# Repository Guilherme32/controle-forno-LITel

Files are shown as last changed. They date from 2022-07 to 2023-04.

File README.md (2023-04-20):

# Controle do forno do LITel

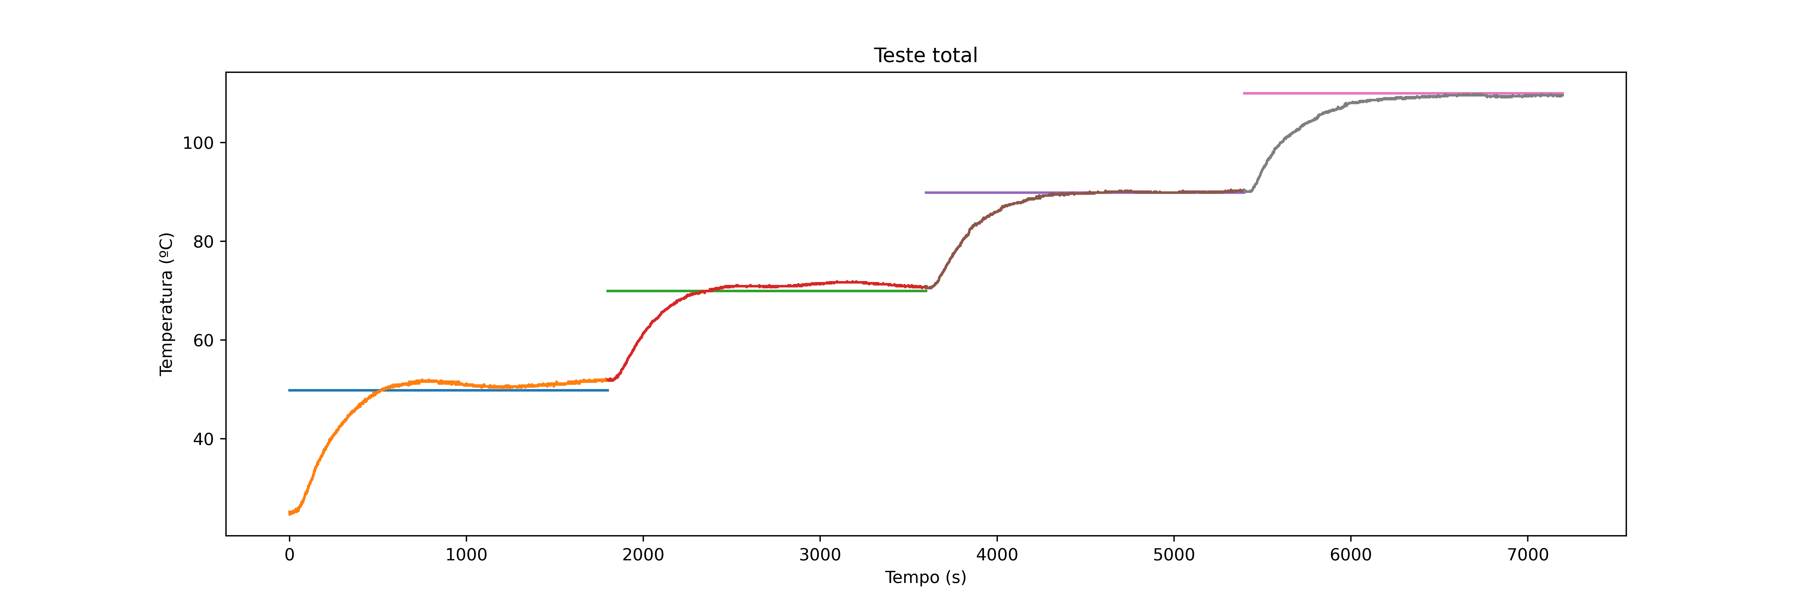
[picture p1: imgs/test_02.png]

Último teste realizado (14/10/2022)

Esse repositório guarda o que foi desenvolvido para o controle do forno do
Laboratório de Instrumentação e Telemetria da UFJF (LITel)

# Informações

O sistema funciona aplicando um controle por lógica Fuzzy (FLC), com modulação
de potência por detecção de zero, para manter a temperatura vista pelo sensor
central do forno no valor especificado. Também pode funcionar por potência fixa.

> Este README contém algumas informações básicas do controlador, e uma
explicação das interfaces de comunicação. *Assim, possui o necessário para
utilizar o projeto*. Maiores detalhes do funcionamento de outras partes podem
ser encontradas no **manual.md** e também na documentação dos códigos.

Para interação com o usuário existem duas interfaces de comunicação:
- WiFi
- Serial

# Comunicação WiFi

Para se comunicar com o controlador por wifi, basta estar na mesma rede. Para
isso, deve-se conectar no ponto de acesso do esp ou estar na rede em que ele
estiver conectado.

Uma vez conectado à mesma rede do esp, o programa pode ser controlado através
das páginas acessíveis em **http://\<endereço ip\>** ou  **\<endereço ip\>:80**.
O endereço depende de qual interface wifi está sendo utilizada.

## Ponto de Acesso (Access Point)

O esp está configurado para funcionar em modo "access point", permitindo que
dispositivos se conectem a ele. As credenciais de acesso são:

> SSID: forno-litel
>
> Senha: 787Cu7kg

Nesse modo, o programa pode ser acessado pelo ip:

> ip: 192.168.4.1

## Modo Estação (station)

Nesse modo, o esp tentará se conectar à rede que estiver configurado para se
conectar. A única forma de alterar essa configuração é pelas próprias páginas
web.

> Ao mudar a configuração, ele automaticamente irá se desconectar da rede em
que estava anteriormente. Logo a forma mais indicada de fazer essa alteração é
acessando através do ponto de acesso.

O ip quando nesse modo depende do roteador (ou ponto de acesso no geral) em que
está se conectando. Esse ip será informado na página de conexão e também pode
ser descoberto pelo comando serial **!netinfo**.

## Páginas

### Página Principal

A página principal serve apenas como uma entrada à interface. Ela permite acesso
às outras páginas do sistema, e também linka para esse repositório.

> Todas as outras páginas possuem também links para as outras páginas do sistema
e para esse repositório.

### Conexão

Essa página mostra as informações de conexão (SSID, senha, ip), e permite mudar
as credenciais da rede a ser acessada pelo modo estação.

> No caso do modo estação, a página também indica se o esp está devidamente
conectado

### Controle

Essa é a página mais importante, e também a mais pesada. É normal que ela demore
muitos segundos para carregar.

> Se a página estiver apresentando instabilidades, por favor reporte para mim ou
crie um "issue" aqui no repositório

A página possui alguns componentes:

- Operação: 
    O forno pode funcionar por potência fixa ou por set point. Uma vez que
    o modo é selecionado, e o valor desejado inserido na caixa de texto, o botão
    enviar pode ser pressionado para enviar as informações para o
    microcontrolador.

- Informações instantâneas:
    Para melhor entendimento, algumas informações são colocadas referentes ao
    funcionamento do forno no último instante recebido.
    - A potência enviada às resistências;
    - Se o sistema está em regime transitório ou alcançou o estacionário;
    - A temperatura no sensor principal (S5, o que fica no centro).

- Gráfico:
    Um gráfico temporal com os valores de set point (se estiver no modo de
    controle) e os valores lidos por todos os sensores. Cada conjunto pode ser
    apagado ou redesenhado para maior clareza. Também, vale notar que o gráfico
    somente mostra as últimas 240 amostras.

> O gráfico e as informações instantâneas são atualizados com 5 segundos. Dessa
forma, o gráfico mostra amostras dos últimos 20 minutos.

# Comunicação Serial

A interface serial funciona utilizando uma taxa (baud rate) de **115200 bits/
s**, com 8 bits de dados e 1 de parada (stop bit).

A comunicação ocorre através de comandos. Para enviar um comando, deve-se enviar
primeiro um caracter de início (!), então escrever o comando, seguido pelo
argumento, caso exista, seguindo a formatação exigida.

Os comandos implementados são:
- **!netinfo**: Devolve as informações de rede:
    - SSID, senha e ip do modo ap;
    - Se estiver devidamente conectado no modo sta, SSID e IP desse modo;
    - Se não estiver, indica que o sta está desconectado;

- **!tempX**, onde X é o índice do sensor: Devolve a temperatura lida no sensor
de índice X;

- **!sensorX**, onde X é o índice do sensor: Parecido com o **temp**, mas
retorna o inteiro entre 0 e 1023 que representa a leitura crua do adc (analog -
digital converter) do esp;

- **!settXXX.X**, onde XXX.X é a temperatura em ºC, com três dígitos antes
da vírgula, e um depois: Seta o set point do sistema de controle para o valor
de temperatura passado. Para não alcançar a temperatura máxima de operação do
sensor, o valor máximo que pode ser passado é 140ºC. Automaticamente ativa o
modo de controle;

- **!setpXXX**, onde XXX é um inteiro representando a quantidade de semiciclos
ligados: Seta a relação de potência a ser enviada para as resistências. O
período da modulação de potência é de 120 semiciclos, logo o valor enviado deve
estar entre 0 e 120 (inclusivo), onde 0 é carga desligada e 120 é carga em plena
potência. Automaticamente ativa o modo de potência fixa;

> A formatação dos argumentos deve ser exatamente como descrita, ou o programa
pode não responder adequadamente

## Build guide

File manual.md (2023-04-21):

# Manual de Referência do Sistema de Controle Do Forno LITel

O sistema de controle foi desenvolvido com um microcontrolador, um esp8266,
programado em c com uso do sdk da fabricante com sistema operacional [ESP8266
RTOS SDK](https://github.com/espressif/ESP8266_RTOS_SDK). Para o desenvolvimento
da placa de circuito impresso (PCB), foi utilizado o
[KiCad](https://www.kicad.org), um programa de Automação de Design Eletrônico
(EDA) open source.

A parte física pode ser dividida em algumas seções, que foram também separadas
para maior clareza no esquemático do circuito (kicad/projeto/projeto.kicad_sch):

# Divisão da parte física

## Sensor

O esp8266 possui apenas um conversor analógico - digital (adc), portanto foi
necessário o uso de um multiplexador analógico (CD4051) para permitir a leitura
de todos os sensores. Também, o adc suporta até 1V, enquanto o sensor pode
enviar até 1.5V. Um divisor de tensão foi utilizado para reduzir essa pela
metade, se encaixando com folga nos limites do microcontrolador.

O adc possui uma precisão de 10 bits, ou 1024 valores. Isso significa uma
precisão de 1/1024 = 0.977mV. O sensor utilizado (LM35) entrega 10mV/ºC, com
precisão típica entre 0.2ºC -> 2mV e 0.4ºC -> 4mV.

Os sensores são:
- S1: Central do fundo
- S2: Lateral direito
- S3: Lateral esquerdo
- S4: Porta
- S5: Principal (centro)
- S6: Ambiente

> No software, os sensores são indexados a partir de 0, não 1, logo o índice
será o descrito aqui menos 1.

## Status

Para visualização de alguns parâmetros diretamente na placa, três leds são
utilizados:

- Steady State: Liga quando a temperatura alcança um regime permanente;

- Wifi Status: Indica o status do modo estação do esp. Enquanto está tentando se
conectar, o led pisca. Se falhar / enquanto não estiver conectado devidamente,
fica desligado. Quando ligado e funcionando, fica ligado;

- Ligado: Liga diretamente na linha de 3.3V da placa, indicando quando o sistema
está energizado.

## Botões (Buttons)

Alguns botões são necessários para o adequado funcionamento, principalmente
para desenvolvimento.

- Reset: O botão para resetar o esp;
- Exit: Esse botão é ligado no pino de flash do esp, que deve ser mantido
em nível lógico baixo (pressionado) ao ligar para permitir o upload de novo
firmware.

## Detecção de Zero (Zero Detection)

Para a estratégia de modulação implementada, é necessário que o microcontrolador
saiba exatamente quando a tensão CA cruza 0V. Essa seção do circuito utiliza
um diodo zener e um optoacoplador (4N25) para gerar um pulso exatamente nesse
momento.

> O diodo zener foi utilizado para aumentar a largura do pulso, que não estava
sendo detectado de forma consistente em testes com apenas o optoacoplador.

## Driver da Carga (Load Driver)

Essa parte é a responsável por ativar a resistência da saída, através do uso
de um optoacoplador, que permite a condução entre o Gate e o terminal A2,
logo ativando a condução do triac, quando recebe um sinal de nível alto do
microcontrolador.

## Alimentação (Power)

O circuito é alimentado com 5V, que pode vir tanto do conversor USB-serial (se
estiver sendo utilizado) quanto de uma alimentação externa com um conector CC de
2.5mm. Os capacitores são utilizados para reduzir ruído da fonte e para garantir
que, caso o microcontrolador consuma uma corrente mais alta do que a fonte /
conversor são capazes de suprir por um curto período de tempo, o circuito ainda
funcione.

> Embora o esperado seja 5V, a fonte pode ser de até 10V, e os circuito ainda
funcionará adequadamente. Porém, vale notar que, se o circuito for alimentado
por uma fonte externa, ele **não deve ser alimentado pela tensão do conversor
USB-serial**. Nesse caso ainda deve se ligar o gnd do serial.

A alimentação CA é para a carga, e é protegida por um fusível (o instalado na
montagem foi de 12A).

## Serial

Aqui há apenas a conexão direta entre os pinos de comunicação serial do
microcontrolador com dois pinos (TX, RX), e a conexão da alimentação também em
dois pinos (5V, GND)

> Ao longo de todo o circuito, estão presentes diversos jumpers. Esses foram
usados apenas para facilitar a construção da PCB

# O Software

Para o projeto, foram desenvolvidos códigos para o microcontrolador (software
embarcado), para automatizar tarefas, e para interface com o usuário com uma
página web.

O código da página web foi desenvolvido em html, css e js, apenas como um
supervisório, e os detalhes de seu conteúdo podem ser vistos nos README.md e
também nas documentações e comentários dentro dos códigos.

O código para automatizar o envio dos arquivos web para o esp está em codigo/
helpers.

O software embarcado foi todo desenvolvido para ser concorrente, por meio do
sistema operacional FreeRTOS, embutido no
[SDK utilizado](https://github.com/espressif/ESP8266_RTOS_SDK), a esp-idf
(SDK da fabricante). Cada parte do sistema foi implementada em um arquivo .c
separado, e todas são inicializadas no main.c. Para os sistemas que dependem de
uma task, essas também são criadas no main.

> Para mais detalhes em qualquer código, basta abrir e ler os comentários e
documentações das funções. As documentações se encontram nos headers (.h) para
funções públicas, e nos source (.c) para as estáticas.

- main: O ponto de entrada do programa do microprocessador. Inicializa cada
parte individual do sistema, e cria as tasks para os que precisam de uma criada;

- wifi: Cuida da conexão WiFi do esp8266, tanto a inicialização do modo *Access
Point* quanto de tentar conectar a uma rede externa no modo *Station*;

- sensor_reader: Responsável por fazer a leitura periódica dos sensores e manter
seus valores acessíveis a outras partes do programa;

- serial_comm: Trata as entradas recebidas na porta serial, e ativa os devidos
comandos quando os seus padrões forem detectados;

- server: Implementa o servidor HTTP que serve como interface principal do
sistema;

- storage_spiffs: Faz a inicialização (mount) do sistema de arquivos usado
(SPIFFS). O sistema de arquivos é utilizado apenas para guardar os arquivos
web;

- helpers: Possui funções independentes que podem ser úteis em diversas partes
do programa, apenas para evitar reescrevê-las;

## controller

Essa seção é responsável por enviar à carga a potência desejada, e também por
periodicamente invocar controlador propriamente dito (que toma a decisão). O
algoritmo de modulação de potência utilizado foi um baseado no por detecção
de zero (*Zero Detection*). O mais comumente visto dessa técnica é permitir
a condução em X semiciclos, enquanto bloqueia a condução em Y. A condução do
dispositivo é sempre acionada quando  tensão cruza 0V, garantindo o mínimo
possível de perdas por chaveamento e também permitindo mais precisão na potência
controlada, se comparado ao método por PWM, por exemplo (considerando carga
atendida em CA acionada por um TRIAC). O que difere no método utilizado é a
distribuição dos semiciclos de condução e corte, que não mais são consecutivos
no período de funcionamento.

No método utilizado, a potência é representada por dois valores (X, Y), onde
X é a quantidade de semiciclos de condução, Y a quantidade de semiciclos em
corte, e X+Y o período total. Para determinar o que deve ser o semiciclo atual,
uma variável é inicializada em 0 e armazenada, chamada de contador de potência
(*power_counter*). Sempre que a borda entre dois semiciclos é percebida (V cruza
0V), o algoritmo define o tipo de semiciclo seguindo o seguinte pseudocódigo:

- Se **contador** > 0:  
    **contador** -= Y  
    **saída** = condução  
- Se **contador** \<= 0:  
    **contador** += x  
    **saída** = corte

Esse código mantém a relação de potência, mas torna a distribuição mais
homogênea. Vale notar que ao final do período (X+Y semiciclos), o contador de
potência é sempre 0. Isso permite uma troca de potência sem efeitos colaterais
de causados por um valor inicial desse contador, caso a mudança seja feita nesse
momento.

### Um pequeno exemplo parar ilustrar a modulação

Potência modulada para 60%, com período de 5 semiciclos:

X = 3, Y = 2

| semiciclo | contador | contador' | saída |  
| --- | --- | --- | --- |
| 0 | 0 | 3 | corte |
| 1 | 3 | 1 | condução |
| 2 | 1 | -1 | condução |
| 3 | -1 | 2 | corte |
| 4 | 2 | 0 | condução |

## fuzzy_controller

Essa parte é a que de fato implementa o sistema de controle. Ela implementa,
como o nome sugere, um controlador de lógica difusa (Fuzzy Logic
Controller - FLC). O controlador foi baseado no de primeira ordem utilizado no
trabalho original de controle do forno
([TCC de Leonardo Serapião](https://www.ufjf.br/mecanica/files/2016/07/Trabalho-de-Conclus%c3%a3o-de-Curso-Leonardo-Ara%c3%bajo-Serapi%c3%a3o-Engenharia-Mec%c3%a2nica.pdf)).
Controladores difusos possuem bom desempenho para controle de sistemas não
lineares, e com possíveis perturbações externas, que é exatamente a situação do
controle de temperatura de um forno.

A lógica difusa funciona de forma parecida com uma lógica digital, porém com
saltos suaves entre variáveis. As variáveis difusa podem assumir valores entre
0 e 1, representando o nível de pertencimento do valor ao espaço da variável.
Esse valor será chamado de $\mu$. Em uma lógica binária, o valor seria 0 ou 1,
representando que pertence ao espaço ou não, não o quanto pertence.

### O controle

O controle se dá da seguinte maneira:

Primeiro, para cada entrada, o seu valor é codificado em algumas variáveis
fuzzy, através de um processo chamado de fuzzificação.

Essas variáveis difusas são então passadas por diversas regras, similares e
análogas a circuitos lógicos, que determinam novas variáveis difusas de saída em
função das de entrada. Cada regra mapeia um conjunto de variáveis de entrada a
uma única variável de saída, mas mais de uma regra pode usar a mesma variável de
saída, neste caso devem ser combinadas.

As variáveis de saída são transformadas em um único valor real (y), em um
processo chamado de defuzzificação.

### Entrada

Para a entrada, dois valores foram analisados: O erro e a variação da
temperatura. O erro é definido como $e[n] = T[n] - T_{set}$, onde $T_{set}$ é a
temperatura alvo. A variação foi pega diretamente da temperatura, e não variação
do erro, para evitar uma descontinuidade quando o set point é trocado. Em
qualquer momento diferente desse, as duas grandezas são equivalentes. Ademais, a
variação de temperatura é analisada ao longo do período de chamada do algoritmo
de controle (30 segundos).

> Na verdade, para facilitar os cálculos, todo o controlador foi implementado
com inteiros, logo a temperatura, variação e alvo são todos em termos da leitura
no ADC, e as variáveis difusas variam entre 0 e 256, em vez de de 0 a 1. A ideia
ainda é a mesma, o que muda é que essas questões devem ser levadas em conta em
algumas operações.

Para a variação da temperatura ($\Delta T$), 3 variáveis foram definidas: N
(negative), Z (zero), P (positive). Para o erro ($e_T$), foram definidas 5:
NL (negative large), NM (negative medium), NS (negative small), Z (zero) e P
(positive). Para ambas, a fuzzifição foi singleton com funções de participação
(*membership functions*) triangulares. Os limites podem vistos nos gráficos:

![Participação para variáveis de Delta T](/imgs/deltaT.svg "Participação para
variáveis de Delta T")

![Participação para variáveis de erro](/imgs/erro.svg "Participação para
variáveis de erro")

### Regras
A saída é composta de duas parcelas, uma que proporciona funções proporcional
e derivativa, a principal, e outra acumuladora de erro (integradora). Para esse
primeiro, as variáveis estabelecidas foram Z (zero), ST (estabilização), baixo
(L), médio (M) e alto (H).

- Se $e_T$ é P, Y é Z
- Se $\Delta_T$ é P, Y é Z

---

- Se $e_T$ é Z, Y é ST
- Se $e_T$ é NS e $\Delta_T$ é P, Y é ST

---

- Se $e_T$ é NM, Y é L
- Se $e_T$ é NS e $\Delta_T$ é Z, Y é L

---

- Se $e_T$ é NL, Y é M
- Se $e_T$ é NM e $\Delta_T$ é Z, Y é M

---

- Se $e_T$ é NL e $\Delta_T$ é Z, Y é H

---

Para o integrador, as variáveis são N (negativo), Z (zero) e P (positivo). A
saída das regras aplicadas é somada com a saída atual para encontrar o novo
valor. O acumulador só funciona a cada 4 ciclos de controle, visto que um
integrador rápido poderia inserir instabilidade no sistema.

- Se $\Delta_T$ é Z e $e_T$ é P, $Y_i$ é N

---

- Se $e_T$ é Z, $Y_i$ é Z
- Se $\Delta_T$ é N ou P, $Y_i$ é Z

---

- Se $\Delta_T$ é Z e $e_T$ é N, $Y_i$ é P

---

> As regras com mesma variável de saída foram combinadas com um OU

### Operações usadas
Foram consideradas as seguintes definições para os operadores:
- A OU B: O maior valor entre A e B;
- A E B: O menor valor entre A e B.

### Saída

A saída de cada parte é então calculada encontrando a centroide de cada
variável de saída, com pesos relativos aos seus valores, e centros considerados
nos pontos centrais das funções de participação, e somada à saída do último
instante. As funções de participação das variáveis de saída podem ser vistas
no gráfico:

Participação para variáveis de saída da parte principal

Para a participação de cada variável que não Z foi somado um valor de correção.
A perda de calor aumenta conforme a diferença entre a temperatura do forno e
externa aumenta. Esse valor ajuda a mitigar esse efeito. Ele é calculado em
tempo real usando a diferença entre o set point e a temperatura ambiente.

Participação para variáveis de saída da parte integradora

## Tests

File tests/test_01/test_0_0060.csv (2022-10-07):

 | S1 | S2 | S3 | S4 | S5 | S6 | set_point | power | time
0 | 21.4844 | 20.1172 | 24.2188 | 20.7031 | 22.4609 | 19.9219 | 59.9609 | [20, 100] | 1.9346058368682861
1 | 21.4844 | 18.75 | 19.3359 | 22.2656 | 22.4609 | 20.3125 | 59.9609 | [20, 100] | 3.1202080249786377
2 | 20.7031 | 18.9453 | 21.875 | 17.5781 | 20.7031 | 21.6797 | 59.9609 | [20, 100] | 4.3214099407196045
3 | 25.3906 | 21.0938 | 25.0 | 21.875 | 20.3125 | 19.9219 | 59.9609 | [20, 100] | 5.475811958312988
4 | 25.9766 | 21.2891 | 20.3125 | 19.3359 | 21.0938 | 20.5078 | 59.9609 | [20, 100] | 6.84861421585083
5 | 19.3359 | 21.0938 | 20.7031 | 17.9688 | 21.2891 | 22.4609 | 59.9609 | [20, 100] | 8.003016710281372
6 | 17.9688 | 20.1172 | 19.5313 | 17.1875 | 22.4609 | 21.6797 | 59.9609 | [20, 100] | 9.157418727874756
7 | 21.6797 | 21.875 | 24.6094 | 19.7266 | 20.3125 | 22.8516 | 59.9609 | [20, 100] | 10.31182050704956
8 | 21.875 | 23.4375 | 15.0391 | 18.9453 | 20.1172 | 16.7969 | 59.9609 | [20, 100] | 11.466222524642944
9 | 20.5078 | 20.5078 | 18.75 | 19.1406 | 22.6563 | 20.1172 | 59.9609 | [20, 100] | 12.636224746704102
10 | 20.3125 | 22.8516 | 19.3359 | 19.7266 | 19.5313 | 20.3125 | 59.9609 | [20, 100] | 14.024627208709717
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

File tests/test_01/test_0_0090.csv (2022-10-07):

 | S1 | S2 | S3 | S4 | S5 | S6 | set_point | power | time
0 | 40.8203 | 38.6719 | 45.5078 | 52.7344 | 63.4766 | 22.2656 | 89.8438 | [19, 101] | 1.2800040245056152
1 | 41.0156 | 38.6719 | 45.7031 | 52.7344 | 63.4766 | 22.4609 | 89.8438 | [19, 101] | 2.4200055599212646
2 | 40.8203 | 38.6719 | 45.7031 | 52.9297 | 63.6719 | 22.2656 | 89.8438 | [19, 101] | 3.5900073051452637
3 | 41.0156 | 38.6719 | 45.7031 | 52.9297 | 63.6719 | 22.2656 | 89.8438 | [19, 101] | 4.74000883102417
4 | 40.8203 | 38.6719 | 45.5078 | 52.9297 | 63.6719 | 22.2656 | 89.8438 | [19, 101] | 5.880010366439819
5 | 40.8203 | 38.8672 | 45.5078 | 52.7344 | 63.6719 | 22.4609 | 89.8438 | [19, 101] | 7.030012130737305
6 | 41.0156 | 38.8672 | 45.7031 | 52.9297 | 63.6719 | 22.2656 | 89.8438 | [19, 101] | 8.170013666152954
7 | 41.6016 | 38.6719 | 45.5078 | 52.9297 | 63.6719 | 22.4609 | 89.8438 | [19, 101] | 9.32001519203186
8 | 40.8203 | 38.6719 | 45.7031 | 53.125 | 63.8672 | 22.2656 | 89.8438 | [19, 101] | 10.480016946792603
9 | 40.8203 | 38.6719 | 45.7031 | 53.125 | 63.8672 | 22.0703 | 89.8438 | [19, 101] | 11.620018482208252
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

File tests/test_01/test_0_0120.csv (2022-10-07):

 | S1 | S2 | S3 | S4 | S5 | S6 | set_point | power | time
0 | 52.3438 | 49.2188 | 60.9375 | 72.0703 | 91.0156 | 22.0703 | 119.922 | [26, 94] | 1.3500046730041504
1 | 52.3438 | 49.2188 | 60.9375 | 72.2656 | 91.0156 | 22.0703 | 119.922 | [26, 94] | 2.5300064086914062
2 | 52.3438 | 48.8281 | 60.5469 | 72.0703 | 90.8203 | 22.0703 | 119.922 | [26, 94] | 3.6800079345703125
3 | 52.3438 | 49.2188 | 60.9375 | 72.2656 | 91.0156 | 22.0703 | 119.922 | [26, 94] | 4.950009822845459
4 | 52.3438 | 49.2188 | 60.5469 | 72.2656 | 90.8203 | 22.2656 | 119.922 | [26, 94] | 6.170034885406494
5 | 52.3438 | 49.2188 | 60.5469 | 72.2656 | 90.8203 | 22.0703 | 119.922 | [26, 94] | 7.326040267944336
6 | 52.1484 | 49.2188 | 60.5469 | 72.0703 | 90.8203 | 22.0703 | 119.922 | [26, 94] | 8.626042127609253
7 | 52.1484 | 48.8281 | 60.5469 | 72.0703 | 90.625 | 22.0703 | 119.922 | [26, 94] | 9.886043787002563
8 | 52.1484 | 49.2188 | 60.5469 | 72.2656 | 90.8203 | 22.0703 | 119.922 | [26, 94] | 11.127045631408691
9 | 52.1484 | 48.8281 | 60.5469 | 72.0703 | 90.8203 | 21.875 | 119.922 | [26, 94] | 12.26704716682434
10 | 52.1484 | 49.2188 | 60.5469 | 72.0703 | 90.8203 | 22.2656 | 119.922 | [26, 94] | 13.517049074172974
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

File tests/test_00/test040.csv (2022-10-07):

 | S1 | S2 | S3 | S4 | S5 | S6 | set_point | time
0 | 23.0469 | 23.0469 | 25.1953 | 0.585938 | 26.5625 | 0.585938 | 39.8438 | 1.2948023080825806
1 | 23.0469 | 22.6563 | 25.0 | 0.976563 | 26.3672 | 0.976563 | 39.8438 | 2.4648044109344482
2 | 23.4375 | 22.8516 | 25.0 | 0.78125 | 26.7578 | 0.585938 | 39.8438 | 3.853206753730774
3 | 23.4375 | 23.0469 | 25.0 | 0.78125 | 26.5625 | 0.390625 | 39.8438 | 5.023208856582642
4 | 23.4375 | 23.4375 | 25.0 | 0.976563 | 26.7578 | 0.585938 | 39.8438 | 6.27121102809906
5 | 23.0469 | 22.6563 | 24.8047 | 1.17188 | 26.3672 | 1.5625 | 39.8438 | 7.472413063049316
6 | 23.4375 | 23.6328 | 25.0 | 0.78125 | 26.5625 | 0.195313 | 39.8438 | 8.829615473747253
7 | 23.4375 | 23.4375 | 24.8047 | 0.585938 | 26.5625 | 0.390625 | 39.8438 | 9.984017491340637
8 | 23.6328 | 23.4375 | 24.8047 | 0.78125 | 26.3672 | 0.585938 | 39.8438 | 11.200819730758667
9 | 23.6328 | 23.4375 | 24.8047 | 1.36719 | 26.5625 | 0.976563 | 39.8438 | 12.339621782302856
10 | 23.6328 | 23.4375 | 25.0 | 0.195313 | 26.5625 | 0.78125 | 39.8438 | 13.478423714637756
11 | 23.4375 | 23.4375 | 24.8047 | 0.390625 | 26.5625 | 0.976563 | 39.8438 | 14.835626125335693
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

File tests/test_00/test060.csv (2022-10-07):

 | Unnamed: 0 | S1 | S2 | S3 | S4 | S5 | S6 | set_point | time
0 | 0 | 29.6875 | 28.9063 | 33.2031 | 1.7578099999999999 | 42.9688 | 0.585938 | 59.9609 | 1802.6299662590027
1 | 1 | 29.8828 | 29.1016 | 33.5938 | 0.976563 | 43.1641 | 0.585938 | 59.9609 | 1803.7999682426453
2 | 2 | 29.4922 | 28.9063 | 33.3984 | 1.36719 | 43.1641 | 0.78125 | 59.9609 | 1804.9543701410294
3 | 3 | 30.0781 | 29.1016 | 33.2031 | 0.390625 | 43.1641 | 0.390625 | 59.9609 | 1806.1711723804474
4 | 4 | 29.6875 | 28.9063 | 33.3984 | 1.36719 | 42.9688 | 0.976563 | 59.9609 | 1807.6219749450684
5 | 5 | 29.8828 | 28.9063 | 33.3984 | 0.585938 | 42.9688 | 0.976563 | 59.9609 | 1808.7763769626615
6 | 6 | 29.8828 | 29.1016 | 33.3984 | 0.585938 | 43.1641 | 0.976563 | 59.9609 | 1809.99317920208
7 | 7 | 29.8828 | 29.1016 | 33.3984 | 0.19531300000000001 | 43.1641 | 0.78125 | 59.9609 | 1811.2723813056946
8 | 8 | 29.8828 | 29.1016 | 33.2031 | 0.390625 | 43.1641 | 1.17188 | 59.9609 | 1812.426783323288
9 | 9 | 29.4922 | 28.9063 | 33.0078 | 0.976563 | 43.3594 | 0.976563 | 59.9609 | 1813.612385392189
10 | 10 | 29.8828 | 29.2969 | 33.3984 | 0.78125 | 43.1641 | 0.585938 | 59.9609 | 1815.0319879055025
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

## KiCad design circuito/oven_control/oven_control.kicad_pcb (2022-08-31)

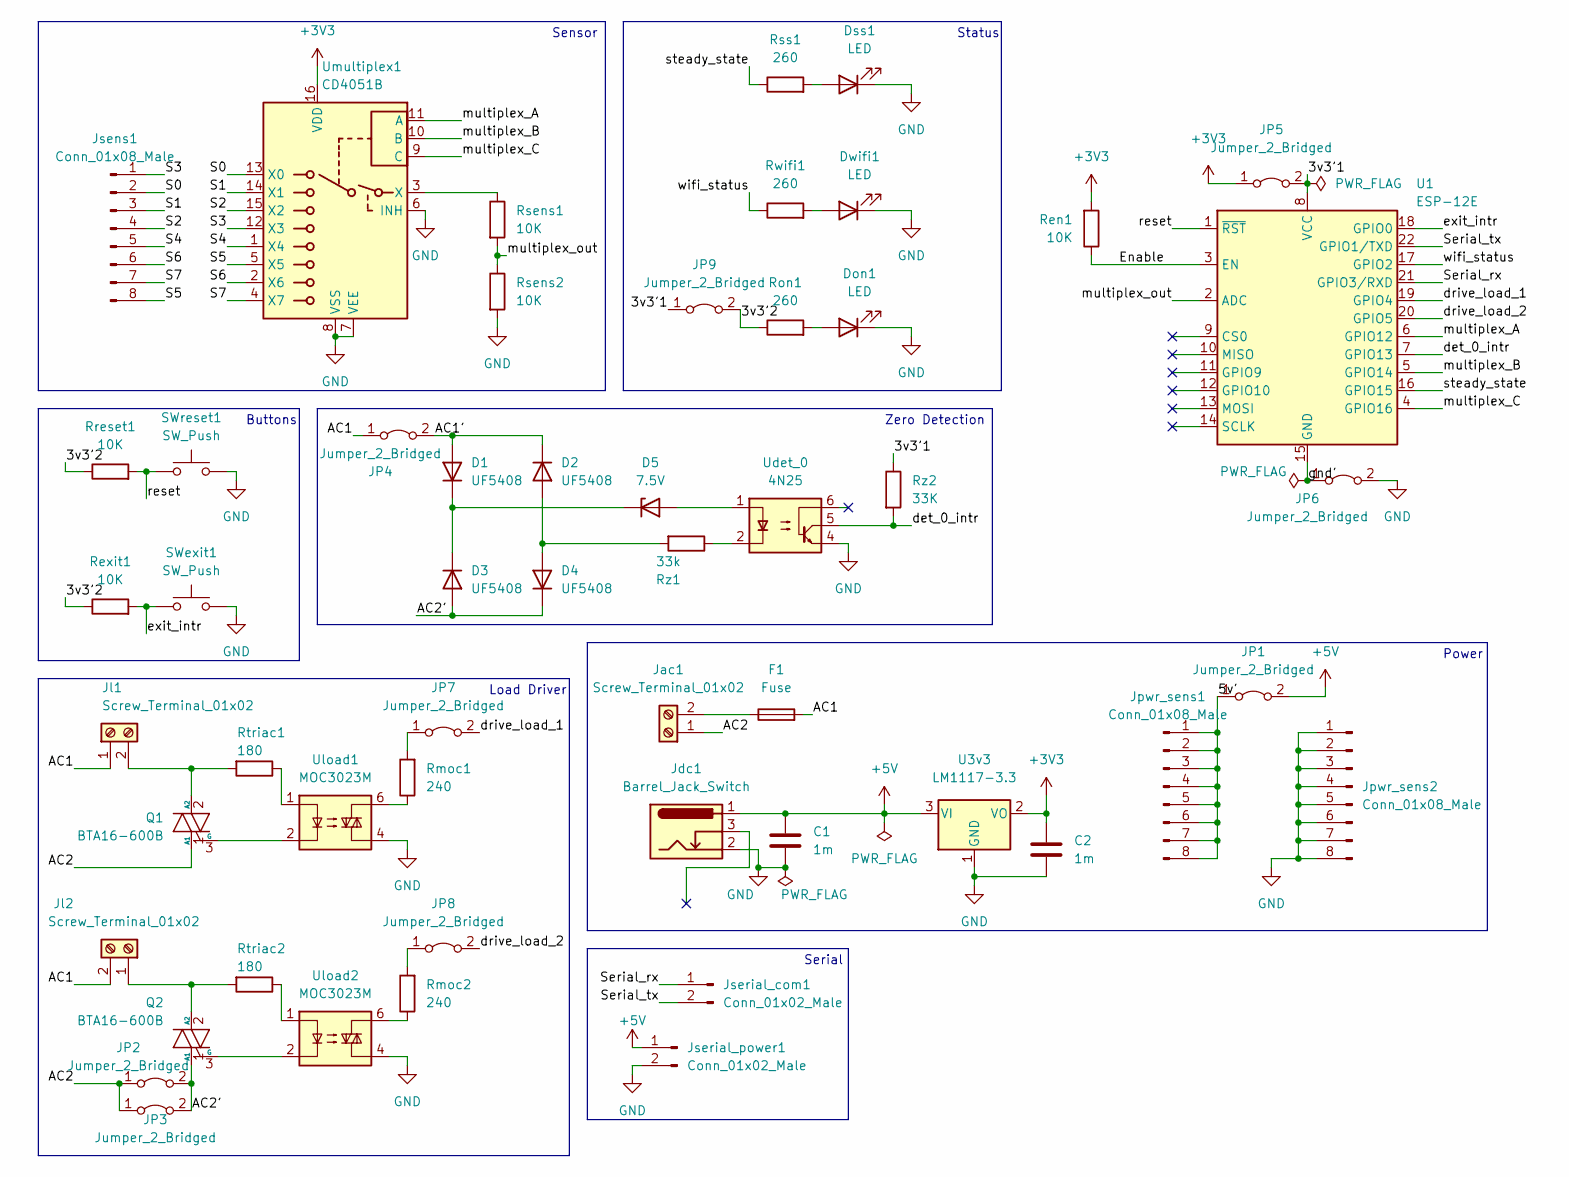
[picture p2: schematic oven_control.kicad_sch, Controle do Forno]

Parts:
C1, C2: 1m; C_Radial_D10.0mm_H16.0mm_P5.00mm
D1, D2, D3, D4: UF5408; D_T-1_P5.08mm_Horizontal
D5: 7.5V; D_T-1_P5.08mm_Horizontal
Don1: LED; LED_D3.0mm
Dss1: LED; LED_D3.0mm
Dwifi1: LED; LED_D3.0mm
F1: Fuse; Fuseholder_Cylinder-5x20mm_Stelvio-Kontek_PTF78_Horizontal_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
JP1, JP2, JP3, JP4, JP5, JP6, JP7, JP8, JP9: Jumper_2_Bridged; jumper_10mm
Jac1: Screw_Terminal_01x02; TerminalBlock_bornier-2_P5.08mm
Jdc1: Barrel_Jack_Switch; BarrelJack_CUI_PJ-102AH_Horizontal
Jl1, Jl2: Screw_Terminal_01x02; TerminalBlock_bornier-2_P5.08mm
Jpwr_sens1, Jpwr_sens2: Conn_01x08_Male; PinHeader_1x08_P2.54mm_Vertical
Jsens1: Conn_01x08_Male; PinHeader_1x08_P2.54mm_Vertical
Jserial_com1: Conn_01x02_Male; PinHeader_1x02_P2.54mm_Vertical
Jserial_power1: Conn_01x02_Male; PinHeader_1x02_P2.54mm_Vertical
Q1, Q2: BTA16-600B; TO-220-3_Vertical
Ren1: 10K; R_Axial_DIN0207_L6.3mm_D2.5mm_P7.62mm_Horizontal
Rexit1: 10K; R_Axial_DIN0207_L6.3mm_D2.5mm_P7.62mm_Horizontal
Rmoc1, Rmoc2: 240; R_Axial_DIN0207_L6.3mm_D2.5mm_P7.62mm_Horizontal
Ron1: 260; R_Axial_DIN0207_L6.3mm_D2.5mm_P7.62mm_Horizontal
Rreset1: 10K; R_Axial_DIN0207_L6.3mm_D2.5mm_P7.62mm_Horizontal
Rsens1, Rsens2: 10K; R_Axial_DIN0207_L6.3mm_D2.5mm_P7.62mm_Horizontal
Rss1: 260; R_Axial_DIN0207_L6.3mm_D2.5mm_P7.62mm_Horizontal
Rtriac1, Rtriac2: 180; R_Axial_DIN0309_L9.0mm_D3.2mm_P12.70mm_Horizontal
Rwifi1: 260; R_Axial_DIN0207_L6.3mm_D2.5mm_P7.62mm_Horizontal
Rz1: 33k; R_Axial_DIN0309_L9.0mm_D3.2mm_P12.70mm_Horizontal
Rz2: 33K; R_Axial_DIN0207_L6.3mm_D2.5mm_P7.62mm_Horizontal
SWexit1: SW_Push; SW_PUSH_6mm
SWreset1: SW_Push; SW_PUSH_6mm
U1: ESP-12E
U3v3: LM1117-3.3; TO-220-3_Vertical
Udet_0: 4N25; DIP-6_W7.62mm_Socket_LongPads
Uload1, Uload2: MOC3023M; DIP-6_W7.62mm_Socket_LongPads
Umultiplex1: CD4051B; DIP-16_W7.62mm_Socket

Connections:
+3V3: C2.1, JP5.1 (A), Ren1.2, U3v3.2 (VO), Umultiplex1.16 (VDD)
+5V: C1.1, JP1.2 (B), Jdc1.1, Jserial_power1.1, U3v3.3 (VI)
/3v3'1: JP5.2 (B), JP9.1 (A), Rz2.1, U1.8 (VCC)
/3v3'2: JP9.2 (B), Rexit1.1, Ron1.1, Rreset1.1
/5v': JP1.1 (A), Jpwr_sens1.1, Jpwr_sens1.2, Jpwr_sens1.3, Jpwr_sens1.4, Jpwr_sens1.5, Jpwr_sens1.6, Jpwr_sens1.7, Jpwr_sens1.8
/AC1: F1.2, JP4.1 (A), Jl1.1, Jl2.2
/AC1': D1.2 (A), D2.1 (K), JP4.2 (B)
/AC2: JP2.1 (A), JP3.1 (A), Jac1.1, Q1.1 (A1)
/AC2': D3.2 (A), D4.1 (K), JP2.2 (B), JP3.2 (B), Q2.1 (A1)
/Enable: Ren1.1, U1.3 (EN)
/S0: Jsens1.2, Umultiplex1.13 (X0)
/S1: Jsens1.3, Umultiplex1.14 (X1)
/S2: Jsens1.4, Umultiplex1.15 (X2)
/S3: Jsens1.1, Umultiplex1.12 (X3)
/S4: Jsens1.5, Umultiplex1.1 (X4)
/S5: Jsens1.8, Umultiplex1.5 (X5)
/S6: Jsens1.6, Umultiplex1.2 (X6)
/S7: Jsens1.7, Umultiplex1.4 (X7)
/Serial_rx: Jserial_com1.1, U1.21 (GPIO3/RXD)
/Serial_tx: Jserial_com1.2, U1.22 (GPIO1/TXD)
/det_0_intr: Rz2.2, U1.7 (GPIO13), Udet_0.5
/drive_load_1: JP7.2 (B), U1.19 (GPIO4)
/drive_load_2: JP8.2 (B), U1.20 (GPIO5)
/exit_intr: Rexit1.2, SWexit1.1, U1.18 (GPIO0)
/gnd': JP6.1 (A), U1.15 (GND)
/multiplex_A: U1.6 (GPIO12), Umultiplex1.11 (A)
/multiplex_B: U1.5 (GPIO14), Umultiplex1.10 (B)
/multiplex_C: U1.4 (GPIO16), Umultiplex1.9 (C)
/multiplex_out: Rsens1.2, Rsens2.1, U1.2 (ADC)
/reset: Rreset1.2, SWreset1.1, U1.1 (~RST)
/steady_state: Rss1.1, U1.16 (GPIO15)
/wifi_status: Rwifi1.1, U1.17 (GPIO2)
GND: C1.2, C2.2, Don1.1 (K), Dss1.1 (K), Dwifi1.1 (K), JP6.2 (B), Jdc1.2, Jpwr_sens2.1, Jpwr_sens2.2, Jpwr_sens2.3, Jpwr_sens2.4, Jpwr_sens2.5, Jpwr_sens2.6, Jpwr_sens2.7, Jpwr_sens2.8, Jserial_power1.2, Rsens2.2, SWexit1.2, SWreset1.2, U3v3.1 (GND), Udet_0.4, Uload1.4, Uload2.4, Umultiplex1.6 (INH), Umultiplex1.7 (VEE), Umultiplex1.8 (VSS)
unnamed: D1.1 (K), D3.1 (K), D5.1 (K)
unnamed: D2.2 (A), D4.2 (A), Rz1.2
unnamed: D5.2 (A), Udet_0.1
unnamed: Don1.2 (A), Ron1.2
unnamed: Dss1.2 (A), Rss1.2
unnamed: Dwifi1.2 (A), Rwifi1.2
unnamed: F1.1, Jac1.2
unnamed: JP7.1 (A), Rmoc1.2
unnamed: JP8.1 (A), Rmoc2.2
unnamed: Jl1.2, Q1.2 (A2), Rtriac1.2
unnamed: Jl2.1, Q2.2 (A2), Rtriac2.2
unnamed: Q1.3 (G), Uload1.2
unnamed: Q2.3 (G), Uload2.2
unnamed: Rmoc1.1, Uload1.6
unnamed: Rmoc2.1, Uload2.6
unnamed: Rsens1.1, Umultiplex1.3 (X)
unnamed: Rtriac1.1, Uload1.1
unnamed: Rtriac2.1, Uload2.1
unnamed: Rz1.1, Udet_0.2

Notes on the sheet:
Status
Power
Serial
Zero Detection
Load Driver
Sensor
Buttons

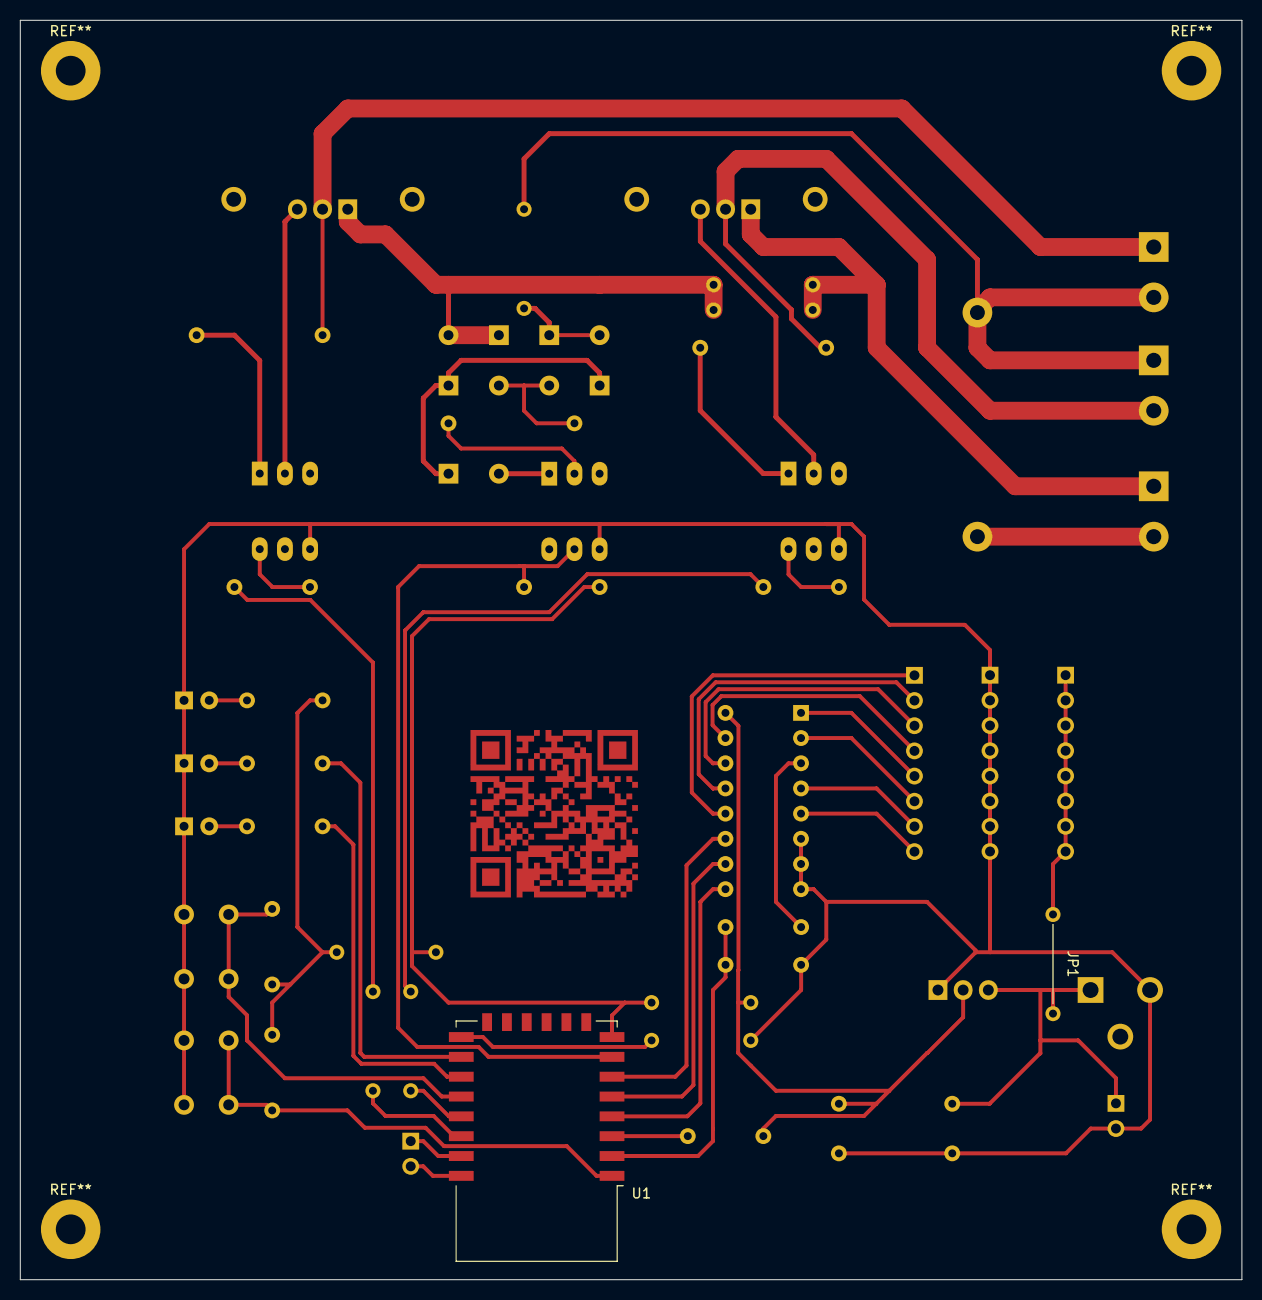
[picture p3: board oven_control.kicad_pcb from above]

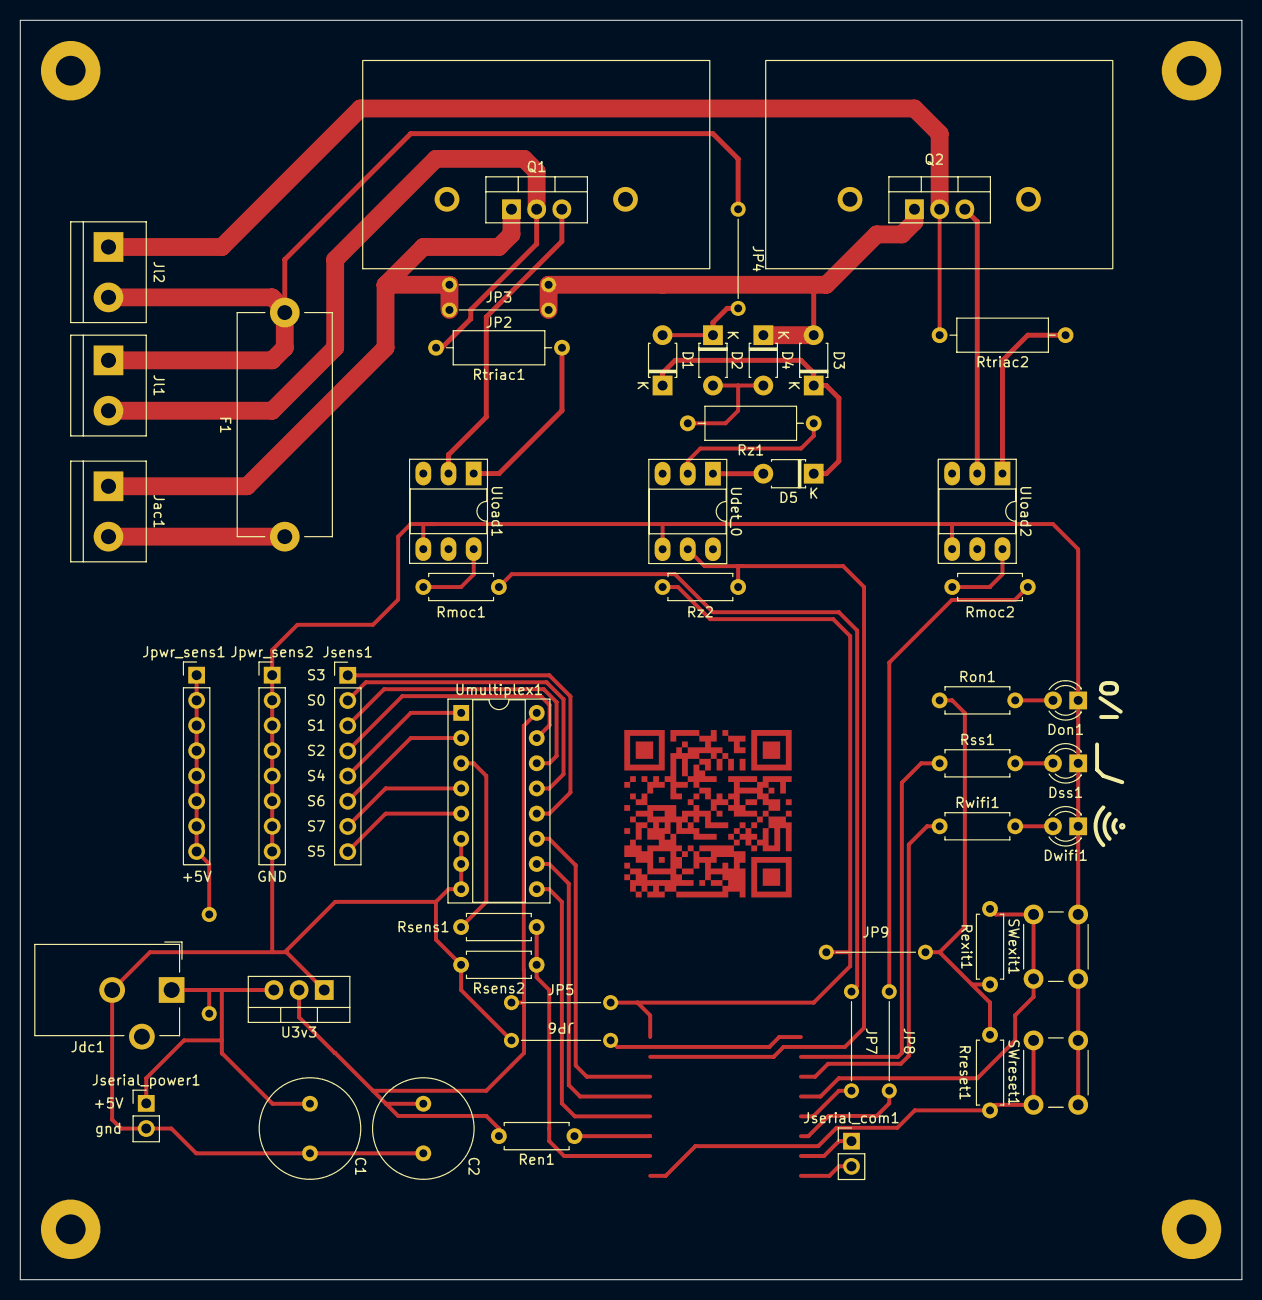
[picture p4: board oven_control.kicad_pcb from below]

Board: 2 copper layers, 123.2 x 127.0 mm, 53 parts (51 on the bottom side), 52 nets.

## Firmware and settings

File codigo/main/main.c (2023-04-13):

/* Hello World Example

   This example code is in the Public Domain (or CC0 licensed, at your option.)

   Unless required by applicable law or agreed to in writing, this
   software is distributed on an "AS IS" BASIS, WITHOUT WARRANTIES OR
   CONDITIONS OF ANY KIND, either express or implied.
*/
#include <stdio.h>
#include "freertos/FreeRTOS.h"
#include "freertos/task.h"
#include "esp_system.h"
#include "esp_spi_flash.h"
#include "esp_log.h"

#include "wifi.h"
#include "server.h"
#include "storage_spiffs.h"
#include "sensor_reader.h"
#include "controller.h"
#include "serial_comm.h"


int main_sensor_reading() {
    return get_reading(4);
}

int ambient_sensor_reading() {
    return get_reading(5);
}

void app_main()
{
    // Some system info print ---------------------------------------------------------------------
    print_header();
    ESP_LOGI("STARTUP", "Starting up the system");

    // Modules init -------------------------------------------------------------------------------
    sensor_init();
    wifi_init();
    spiffs_init();
    server_init(10);
    controller_init(main_sensor_reading, ambient_sensor_reading);
    serial_comm_init();

    // Linking modules ----------------------------------------------------------------------------
    add_command(netinfo_command, netinfo_command_help);
    add_command(set_ratio_command, set_ratio_command_help);
    add_command(set_target_command, set_target_command_help);
    add_command(reading_command, reading_command_help);
    add_command(temperature_command, temperature_command_help);

    // Starting modules tasks ---------------------------------------------------------------------
    xTaskCreate(sensors_task, "sensor_task", configMINIMAL_STACK_SIZE, NULL, 10, NULL);
    xTaskCreate(wifi_led_task, "wifi_led_task", 2*configMINIMAL_STACK_SIZE, NULL, 10, NULL);
    xTaskCreate(serial_comm_task, "serial_task", 2*configMINIMAL_STACK_SIZE, NULL, 10, NULL);
}

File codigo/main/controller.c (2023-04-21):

#include "controller.h"
#include "helpers.h"

// Internal definitions ---------------------------------------------------------------------------

#define INTERRUPT_PIN 13
#define INTERRUPT_PIN_FLAG (1ULL << INTERRUPT_PIN)

#define OUTPUT_PIN_0 4
#define OUTPUT_PIN_1 5
#define STEADY_PIN 15
#define OUTPUT_PINS_FLAG   ( (1ULL << OUTPUT_PIN_0) \
                           | (1ULL << OUTPUT_PIN_1) \
                           | (1ULL << STEADY_PIN))

#define PERIOD 120
#define MAX_TARGET 140
#define MAX_TARGET_READING ((MAX_TARGET * 1023) / 200)
#define STEADY_LIMIT 4
#define STEADY_TIME 60

#define CONTROLLER_TAG "CONTROLLER"


// Global variables declaration -------------------------------------------------------------------

static int power_ratio[2];
static int power_counter;
static int cycles;

static bool control;
static int target;
static bool steady;
static int steady_count;

static unsigned long int last_time;        // In microseconds
static int last_sensor_read;

int (*read_sensor)();
int (*read_ambient)();


// Static functions declaration -------------------------------------------------------------------

/** Atualiza a relacao de ligado/deligado (taxa de potencia) */
static void IRAM_ATTR update_ratio();

/** Funcao inicializada no cruzamento com o zero. Decide se o semiciclo sera ligado ou desligado */
static void IRAM_ATTR send_power();

/** Confere se o sistema alcancou o regime estacionario */
static void IRAM_ATTR check_steady_state();

/** Coloca nos terminais que controla o driver da carga o nivel logico passado.  */
static void IRAM_ATTR set_pins(int level);

/** Confere se o contador de potencia (utilizado na modulacao) esta dentro dos limites. */
static void check_counter_limits();


// Static functions -------------------------------------------------------------------------------

static void IRAM_ATTR update_ratio()
{
    if (control) {
        int accumulate = steady && (abs(read_sensor() - target) > STEADY_LIMIT);
        unsigned int power = run_fuzzy_step(
            read_sensor(),
            read_ambient(),
            accumulate);

        power_ratio[0] = power;
        power_ratio[1] = PERIOD - power;
    }
}

static void IRAM_ATTR send_power()
{
    unsigned long int new_time = esp_timer_get_time();
    unsigned int time_diff = new_time - last_time;

    if (time_diff < 4000) {                 // Debounce
        return;
    }
    last_time = new_time;

    if (power_counter > 0) {                // Actual power control
        power_counter -= power_ratio[1];
        set_pins(1);
    } else {
        power_counter += power_ratio[0];
        set_pins(0);
    }

    if ((cycles % PERIOD) == 0) {           // Steady state checking
        check_steady_state();
    }

    if (cycles >= (30 * PERIOD)) {          // Updates the ratio every 30 modulation PERIODs
        cycles = 0;
        update_ratio();
    }

    cycles ++;
}

static void IRAM_ATTR check_steady_state()
{
    if (abs(read_sensor() - last_sensor_read) <= STEADY_LIMIT) {
        steady_count ++;
    } else {
        last_sensor_read = read_sensor();
        steady_count = 0;
    }

    if (steady_count >= STEADY_TIME) {
        steady = true;
    } else {
        steady = false;
    }

    gpio_set_level(STEADY_PIN, steady);
}

static void IRAM_ATTR set_pins(int level)
{
    // At the moment doesn't support individual load power modulation
    gpio_set_level(OUTPUT_PIN_0, level);
    gpio_set_level(OUTPUT_PIN_1, level);
}

static void check_counter_limits()
{
    power_counter = power_counter >  power_ratio[0]?  power_ratio[0] : power_counter;
    power_counter = power_counter < -power_ratio[1]? -power_ratio[1] : power_counter;
}


// Public functions -------------------------------------------------------------------------------

void set_ratio(int cycles_on)
{
    if ((cycles_on > PERIOD) || (cycles_on < 0)) {
        return;
    }

    power_ratio[0] = cycles_on;
    power_ratio[1] = PERIOD - cycles_on;
    check_counter_limits();
    control = false;
}

void set_target(int _target)
{
    if (_target > MAX_TARGET_READING) {
        ESP_LOGE(CONTROLLER_TAG, "Tried to set a target too high (%d/ %d)",
            _target, MAX_TARGET_READING);
        return;
    }

    target = _target;
    set_fuzzy_target(target);
    control = true;
    update_ratio();
    check_counter_limits();
}

void controller_shutdown()
{
    control = false;
    power_counter = 0;
    power_ratio[0] = 0;
    power_ratio[1] = PERIOD;
    set_pins(0);
}

ControllerInfo controller_info()
{
    ControllerInfo out = {
        .steady = steady,
        .power_ratio = {power_ratio[0], power_ratio[1]},
        .control = control,
        .target = target
    };

    return out;
}

bool set_ratio_command(char* message)
{
    if (strlen(message) != 7) {
        return false;
    }
    if (strncmp(message, "setp", 4) != 0) {
        return false;
    }

    if (!is_number(&message[4], 3)) {
        printf("\nInvalid input. XXX must be a number with three digits (use ");
        printf("zero padding if needed)\n");
        return true;
    }

    int cycles_on = atoi(&(message[4]));
    if ((cycles_on < 0) || (cycles_on > PERIOD)) {
        printf("\nInvalid value. XXX must be between 0 and max period %s",
               "(120 default)\n");
        return true;
    }
    
    set_ratio(cycles_on);
    printf("\nRatio set successfully\n");
    return true;
}

void set_ratio_command_help(char prefix)
{
    printf("%csetpXXX       Sets the number of conducting cycles per period to XXX.\n", prefix);
    printf("               Within [000, 120] by default\n");
}

bool set_target_command(char* message)
{
    if (strlen(message) != 9) {
        return false;
    }
    if (strncmp(message, "sett", 4) != 0) {
        return false;
    }

    if (!is_number(&message[4], 3) || !is_number(&message[8], 1)) {
        printf("\nInvalid input. XXX.X must be a real number following the format, ");
        printf("as 050.1, or 100.0\n");
        return true;
    }

    float target = atof(&(message[4]));
    if (target > MAX_TARGET) {
        printf("\nInvalid value. The max target temperature is %d.0ºC\n", MAX_TARGET);
        return true;
    }

    set_target(target * 1023 / 200);
    printf("\nTarget temperature set successfully\n");
    return true;
}

void set_target_command_help(char prefix)
{
    printf("%csettXXX.X     Sets the target temperature to XXX.XºC.\n", prefix);
    printf("               Within [000.0, %d.0] by default\n", MAX_TARGET);
}
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

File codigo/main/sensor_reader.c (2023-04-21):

#include "sensor_reader.h"


// Definitions ------------------------------------------------------------------------------------

#define CONTROL_PIN_0 12
#define CONTROL_PIN_1 14
#define CONTROL_PIN_2 16
#define CONTROL_PINS_FLAG   ((1ULL << CONTROL_PIN_0) \
                           | (1ULL << CONTROL_PIN_1) \
                           | (1ULL << CONTROL_PIN_2))
#define READ_PERIOD 500
#define MULTISAMPLING 16
#define SENSOR_TAG "SENSOR_READER"

#define TEST_SENSORS_SPEED 0


// Global variables definition --------------------------------------------------------------------

int readings[8] = {0};


// Static functions declaration -------------------------------------------------------------------

/** Transforma uma leitura do sensor em uma temperatura inteira (truncada). */
static int reading_to_temp(int reading);

/**
* Coloca nos pinos de controle o valor adequado. Isso eh feito para acessar os
* sensores com o multiplexador analogico utilizado no circuito
*/
static void set_control_pins(int value);

/** Realiza a leitura de todos os sensores e as armazena na variavel global. */
static void read_temperatures();

/**
* Testa a velocidade de execucao das leituras. Realiza uma serie de leituras.
* Realiza uma longa sequencia de leituras e envia pela serial o tempo de
* execucao.
*/
static void test_speed();



// Static functions definition --------------------------------------------------------------------

static int reading_to_temp(int reading)
{
    // voltage = (reading * 2) / 1023
    // temp = voltage / 0.01
    return (reading * 2  * 100) / 1023;
}

static void set_control_pins(int value)
{
    gpio_set_level(CONTROL_PIN_0, (value >> 0) % 2);
    gpio_set_level(CONTROL_PIN_1, (value >> 1) % 2);
    gpio_set_level(CONTROL_PIN_2, (value >> 2) % 2);
}

static void read_temperatures()
{
    for (int i=0; i<8; i++) {
        set_control_pins(i);
        uint32_t mean = 0;
        uint16_t raw_reading;

        for (int j=0; j<MULTISAMPLING; j++) {
            adc_read(&raw_reading);
            mean += raw_reading;
        }
        mean /= MULTISAMPLING;

        readings[i] = mean;
    }
}

static void test_speed()
{
    uint16_t raw_reading;

    for (int i=0; i<10; i++) {
        uint32_t mean_reading = 0;
        unsigned int start_time = esp_timer_get_time();
    
        for (int j=0; j<1000; j++) {
            adc_read(&raw_reading);
            mean_reading += raw_reading;
        }
    
        mean_reading /= 1000;
        unsigned int end_time = esp_timer_get_time();

        printf("Read 1000 times (mean %u) in %u us\n", mean_reading, 
            end_time-start_time);
    }
}

// Public functions definition --------------------------------------------------------------------

int get_reading(int index)
{
    if (index >= 8 || index < 0) {
        return 0;
    }

    int reading = readings[index];

    return reading;
}

int get_temperature(int index)
{
    if (index >= 8 || index < 0) {
        return 0;
    }

    int reading = get_reading(index);
    return reading_to_temp(reading);
}

bool reading_command(char* message)
{
    if (strlen(message) != 7) {
        return false;
    }
    if (strncmp(message, "sensor", 6) != 0) {
        return false;
    }

    int index = (int)(message[6] - '0');
    if (index < 0 || index > 7) {
        printf("\nInvalid sensor index. The values possible are within [0,8)\n");
    } else {
        printf("\nReading on sensor %u: %u\n", index, get_reading(index));
    }

    return true;
}

void reading_command_help(char prefix)
{
    printf("%csensorX       Displays the ADC reading for sensor X.\n", prefix);
    printf("               Within [0, 8)\n");
}

bool temperature_command(char* message)
{
    if (strlen(message) != 5) {
        return false;
    }
    if (strncmp(message, "temp", 4) != 0) {
        return false;
    }

    int index = (int)(message[4] - '0');
    if (index < 0 || index > 7) {
        printf("\nInvalid sensor index. The values possible are numbers within [0,8)\n");
    } else {
        printf("\nTemperature on sensor %u: %uºC\n", index, get_temperature(index));
    }

    return true;
}

void temperature_command_help(char prefix)
{
    printf("%ctempX         Displays the temperature reading for sensor X, in ºC.\n", prefix);
    printf("               Within [0, 8)\n");
}

void sensor_init()
{
    adc_config_t adc_config;
    adc_config.mode = ADC_READ_TOUT_MODE;
    adc_config.clk_div = 16;
    ESP_ERROR_CHECK(adc_init(&adc_config));

    gpio_config_t gpio_cfg;
    gpio_cfg.intr_type = GPIO_INTR_DISABLE;
    gpio_cfg.mode = GPIO_MODE_OUTPUT;
    gpio_cfg.pin_bit_mask = CONTROL_PINS_FLAG;
    gpio_cfg.pull_down_en = 0;
    gpio_cfg.pull_up_en = 0;
    gpio_config(&gpio_cfg);

    read_temperatures();

    if (TEST_SENSORS_SPEED) {
        test_speed();
    }
}

void sensors_task()
{
    while (1) {
        read_temperatures();
        vTaskDelay(READ_PERIOD / portTICK_PERIOD_MS);
    }
}

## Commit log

2022-06-04 Add Leitor do sensor
    Ainda sem testar, pq depende do multiplex
2022-06-06 Add gerenciador de rede
2022-06-10 Add mais da parte web
    Corrigi o que tinha enviado ate o momento. Agora essa parte ja funciona
2022-06-12 Completar pagina de conexao
2022-06-14 Completar pagina e api de conexão
2022-06-14 Add checagem de estabilidade
2022-06-15 Finalizou a página de controle
2022-06-18 Iniciou o esquemático
    [projeto.kicad_sch]
2022-06-18 Add led de status de conexao
2022-06-18 Finalizou esquematico
    [projeto.kicad_sch]
2022-06-21 Correção de erros do ERC
    [projeto.kicad_sch]
2022-06-22 Att componentes
    [projeto.kicad_sch]
2022-06-23 Fazendo a PCB (1)
    [projeto.kicad_pcb, projeto.kicad_sch]
2022-06-24 Fazendo a PCB
    [projeto.kicad_pcb, projeto.kicad_sch]
2022-06-28 Add qr code
    [projeto.kicad_pcb]
2022-06-28 Add pcb arredondada
    [projeto-F_Cu.gbr, projeto-rounded-B_Silkscreen.gbr, projeto-rounded-Edge_Cuts.gbr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]
2022-06-28 Add alguns dados na pcb
    [projeto.kicad_pcb]
2022-06-29 Fix PCB
    [projeto-B_Silkscreen.gbr, projeto-Edge_Cuts.gbr, projeto-F_Cu.gbr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]
2022-07-02 Renomeações
    [oven_control.kicad_pcb, oven_control.kicad_sch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]
2022-08-31 Fix some errors
    [oven_control.kicad_pcb]
2022-10-07 Improving control and tests
    [test040.csv, test060.csv, test080.csv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]
2022-10-14 making tests
    [test_0_050.csv, test_0_070.csv, test_0_090.csv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]
2023-04-09 Rewriting system in C
    [partitions.csv]
